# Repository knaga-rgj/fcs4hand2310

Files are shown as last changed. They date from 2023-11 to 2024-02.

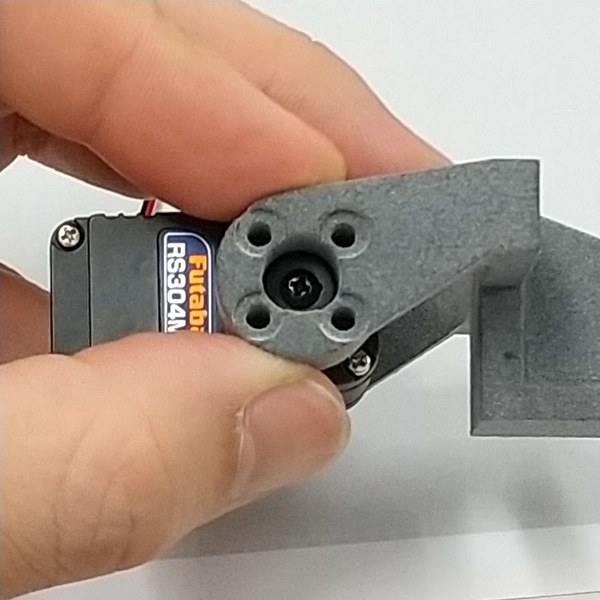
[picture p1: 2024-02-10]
pics/pict11.jpg

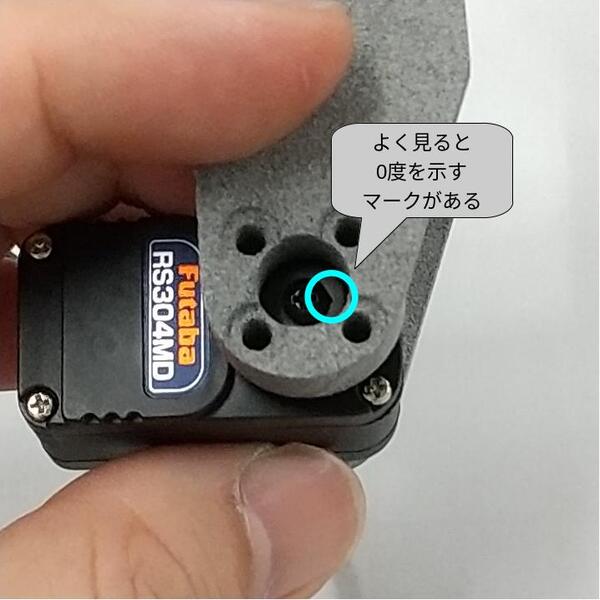
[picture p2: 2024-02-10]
pics/pict08m.jpg

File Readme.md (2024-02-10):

<!-- [GLFM](https://docs.gitlab.com/ee/user/markdown.html)   -->

# fcs4hand2310

## 概要

[双葉電子工業の産業用サーボのコマンド式サーボ](https://www.futaba.co.jp/product/industrial_servo/command_type_servos)を４つ使用するハンドです。

リンク部材は 3D プリンタで作ることを想定しています。（step フォルダ内のデータを活用ください）

ros2_control で制御するために [hardware_fcs](https://github.com/knaga-rgj/hardware_fcs) を使用しています。

各関節角度を joint_trajectory_controller で制御し、joint_state_broadcaster で現在角度を展開するための launch ファイル及び設定ファイル群が用意されています。

humble で動作確認しました。

## 部品一覧

### TTL タイプ

 | 部品名                 | メーカー名   | 型番                                                                                                                                                                                                                                                | 数量   | 備考                                                                                                 |
 |------------------------|--------------|-----------------------------------------------------------------------------------------------------------------------------------------------------------------------------------------------------------------------------------------------------|--------|------------------------------------------------------------------------------------------------------|
 | サーボモジュール       | 双葉電子工業 | [00400021-3 ROBOT SERVO RS304MDFF FUTABA](https://www.futaba.co.jp/product/industrial_servo/command_type_servos/rs304md) もしくは [00400020-3 ROBOT SERVO RS303MRFF](https://www.futaba.co.jp/product/industrial_servo/command_type_servos/rs303mr) | 4      |                                                                                                      |
 | ハブ                   | 双葉電子工業 | [BA2082 TB-RV71EH-7.4V/3W](https://www.futaba.co.jp/product/industrial_servo/command_type_servos/option_parts/relaybox_hub)                                                                                                                         | 1      | 類似型番に注意。末尾「3W」を使用。                                                                   |
 | USB アダプタ           | 双葉電子工業 | [00400070-1 CONVERTER RSC-U485 JPN](https://www.futaba.co.jp/product/industrial_servo/command_type_servos/rsc)                                                                                                                                      | 1      | TB-RV71EH-7.4V/3W とセットで使用（代用不可）                                                         |
 | 電源ケーブル(ハブ側)   | 双葉電子工業 | [BC0079 TB-RV71EH POWER CABLE](https://www.futaba.co.jp/product/industrial_servo/command_type_servos/option_parts/relaybox_hub)                                                                                                                     | 1      | つながれば代用可                                                                                     |
 | EH ４ピンコネクタ      | JST          | [EHR-4](https://www.jst-mfg.com/product/pdf/jpn/EH.pdf)                                                                                                                                                                                             | 4      | ターミネート抵抗を刺すなら１つ追加。                                                                 |
 | EH用コンタクト         | JST          | [(適宜)](https://www.jst-mfg.com/product/pdf/jpn/EH.pdf)                                                                                                                                                                                            | 12     | サーボモジュールは一般的な３ピンで、ハブの４ピンに交換するため。ターミネート抵抗を挿すなら２個追加。 |
 | モータ電源             | (適宜)       | (適宜)                                                                                                                                                                                                                                              | 1      | サーボモジュールは 4.8〜7.2[V] が定格、電流容量は不明                                                |
 | 電源ケーブル（電源側） | (自作)       | (自作)                                                                                                                                                                                                                                              | 1      |                                                                                                      |
 | タッピングネジ         | (適宜)       | (M2 タッピング 10 mm)                                                                                                                                                                                                                               | 34     |                                                                                                      |
 | 両面テープ             | (適宜)       | (薄手のもの)                                                                                                                                                                                                                                        | (適宜) | サーボモジュールとリンク部材との固定は両面テープ                                                     |
 | リンク部材             | (適宜)       | (step ディレクトリ内のを 3D プリント)                                                                                                                                                                                                               | 各1    |                                                                                                      |

工作概略
 - 各サーボモジュールのコネクタを EHR-4 に付け替え
 - リンク部材をサーボホーンにネジ止め
 - リンク部材にサーボモジュールを両面テープで貼り付け
 - 基部のサーボモジュール押さえをネジ止め
 - 電源ケーブル作成（ハブ側、電源側）
 - 配線結線、ID 焼き込み、動作確認
 
注意事項
 - USB アダプタからハブまでは RS-485 なので、ターミネート抵抗を両端に入れると安心できるかもしれません。

### RS-485 タイプ

TTL タイプと比べて RS-485 通信の安心感が増す一方で作業量が増えます。特に DF11 4ピンの配線を間違えると悲惨で危険なことになるかもしれません。

 - サーボモジュールを[外形形状が同じで RS-485 タイプのもの (RS302CD や RS305CR)](https://www.futaba.co.jp/product/industrial_servo/command_type_servos) に変更
 - 軸付きボトムケース [BS3397 RS30x BOTTOM CASE-SHAFT](https://www.futaba.co.jp/product/industrial_servo/command_type_servos/option_parts/servo_caseset) を４つ追加調達
 - フリーホーン（５個セット）[BS0168 RS2xx/RS3xx FREE HORN SET](https://www.futaba.co.jp/product/industrial_servo/command_type_servos/option_parts/servo_horn)を１セット追加調達
 - ハブを[「BA2083 TB-EH31DF-100 もしくは BA2084 TB-EH31DF-200」と「BA2085 TB DF31DF-100」](https://www.futaba.co.jp/product/industrial_servo/command_type_servos/option_parts/relaybox_hub) の２個セットに変更
 - 電源ケーブル（ハブ側）は削除
 - 電源ケーブルを自作（２芯、電源供給側から DF11-4 へ、VCC, GND）
 - 通信用変換ケーブルを自作（３芯、EHR-4 から DF11-4 への変換、D+, D-, GND）

 | 部品名              | メーカー名   | 型番                                                                                                                                                                                                                                   | 数量   | 備考                                                                                                                                                                            |
 |---------------------|--------------|----------------------------------------------------------------------------------------------------------------------------------------------------------------------------------------------------------------------------------------|--------|---------------------------------------------------------------------------------------------------------------------------------------------------------------------------------|
 | サーボモジュール    | 双葉電子工業 | [00400038-1 ROBOT SERVO RS302CDF3 FUTABA ](https://www.futaba.co.jp/product/industrial_servo/command_type_servos/rs302cd) もしくは [00400065-3 RS305CR](https://www.futaba.co.jp/product/industrial_servo/command_type_servos/rs305cr) | 4      |                                                                                                                                                                                 |
 | 軸付きボトムケース  | 双葉電子工業 | [BS3397 RS30x BOTTOM CASE-SHAFT](https://www.futaba.co.jp/product/industrial_servo/command_type_servos/option_parts/servo_caseset)                                                                                                     | 4      |                                                                                                                                                                                 |
 | フリーホーン        | 双葉電子工業 | [BS0168 RS2xx/RS3xx FREE HORN SET](https://www.futaba.co.jp/product/industrial_servo/command_type_servos/option_parts/servo_horn)                                                                                                      | 1      | ５個１セット                                                                                                                                                                    |
 | ハブ（根元側）      | 双葉電子工業 | [BA2083 TB-EH31DF-100 もしくは BA2084 TB-EH31DF-200](https://www.futaba.co.jp/product/industrial_servo/command_type_servos/option_parts/relaybox_hub)                                                                                  | 1      | コネクタを自分で帳尻合わせするなら、創設側と同じ [BA2085 TB DF31DF-100](https://www.futaba.co.jp/product/industrial_servo/command_type_servos/option_parts/relaybox_hub) でも可 |
 | ハブ（増設側）      | 双葉電子工業 | [BA2085 TB DF31DF-100](https://www.futaba.co.jp/product/industrial_servo/command_type_servos/option_parts/relaybox_hub)                                                                                                                | 1      |                                                                                                                                                                                 |
 | USB アダプタ        | 双葉電子工業 | [00400070-1 CONVERTER RSC-U485 JPN](https://www.futaba.co.jp/product/industrial_servo/command_type_servos/rsc)                                                                                                                         | 1      | TB-RV71EH-7.4V/3W とセットで使用します（代用不可）                                                                                                                              |
 | DF11 ４ピンコネクタ | ヒロセ電機   | [DF11-4DS-2C](https://www.hirose.com/ja/product/document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)                                                                                         | 1      | 電源供給ケーブル用。ターミネート抵抗を挿すなら１個追加。                                                                                                                        |
 | DF11用コンタク      | ヒロセ電機   | [(適宜)](https://www.hirose.com/ja/product/document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)                                                                                              | 2      | 同上（ターミネート抵抗を挿すなら２個追加）                                                                                                                                      |
 | モータ電源          | (適宜)       | (適宜)                                                                                                                                                                                                                                 | 1      | サーボモジュールは 4.8〜7.2[V] が定格、電流容量は不明                                                                                                                           |
 | 電源ケーブル        | 自作         | (適宜)                                                                                                                                                                                                                                 |        |                                                                                                                                                                                 |
 | タッピングネジ      | (適宜)       | (M2 タッピング 10mm)                                                                                                                                                                                                                   | 34     |                                                                                                                                                                                 |
 | 両面テープ          | (適宜)       | (薄手のもの)                                                                                                                                                                                                                           | (適宜) | サーボモジュールとリンク部材との固定は両面テープ                                                                                                                                |
 | リンク部材          | (適宜)       | (step ディレクトリ内のを 3D プリント)                                                                                                                                                                                                  | 各1    |                                                                                                                                                                                 |

工作概略
 - 各サーボモジュールのボトムケースを軸付きに交換
   - 配線に目印をつける
   - DF11 ４ピンのハウジングを外す
   - サーボモジュールのボトムケースを交換する
   - DF11 ４ピンのハウジングをとりつける（信号線を挿す場所を間違えないように）
 - リンク部材をサーボホーンにネジ止め
 - リンク部材にサーボモジュールを両面テープで貼り付け
 - 基部のサーボモジュール押さえをネジ止め
 - 電源ケーブル、通信用変換ケーブル作成
 - 配線結線、ID 焼き込み、動作確認

注意事項
 - ターミネート抵抗を RS-485 配線の両端に入れると安心できるかもしれません。
 - ボトムケースを交換する際、DF11 ４ピンコネクタを一旦バラす必要があります。配線の色も同色なため混同しないように細心の注意が必要です。

## 組み立て手順

[写真](./pics/)を参考にしてください。

## 単体動作確認ツール python3 + dicot

[dicot](https://pypi.org/project/dicot/) が便利です。`pip3 install dicot` でインストールできます。
 
[dicot の README.md](https://github.com/lanius/dicot/blob/master/README.md) に目を通した後は、[ソース](https://github.com/lanius/dicot/blob/master/dicot/motors.py) を読むとアクセスしたいプロパティの名称がわかると思います。

シリアルデバイスは dialout group での読み書きが可能なので、Ubuntu の自分自身のユーザアカウントを dialaout グループに追加しておいてください。例えば alice というユーザ名であれば、`sudo adduser alice dialout` を実行し、再起動してください。

### linux で動かす

RSC-U485 は FTDI のドライバ (ftdi_sio) で動きますが、標準の FTDI のドライバには RSC-U485 が登録されていません。手動でその場で動くようにするには以下のコマンドを実行してください。
 
```
$ sudo su
# modrobe ftdi_sio
# echo 1115 0008 > /sys/bus/usb-serial/drivers/ftdi_sio/new_id
```

次回以降の起動時に自動で認識するようにするには、/etc/udev/rules.d 以下に適当な名前のファイルを作成して、以下の記述を書いておいてください。

```
ATTR{idVendor}=="1115", ATTR{idProduct}=="0008", GROUP="dialout", MODE="0660", RUN+="/bin/sh -c '/sbin/modprobe ftdi_sio; /bin/sh -c \"echo 1115 0008\" > /sys/bus/usb-serial/drivers/ftdi_sio/new_id'"
```

### Windows で動かす

多分、ドライバを[Futaba のサイト](https://www.futaba.co.jp/product/industrial_servo/command_type_servos/robot_download/software) からダウンロードしてインストールして、どの COM ポートに割り当てられたか調べて、dicot でその COM ポートを指定すれば動くのではないか、と思います。

## ros2_control で動かすときのコマンドライン覚書

全軸 torque off (inactive 状態へ遷移)

```
ros2 service call /controller_manager/set_hardware_component_state controller_manager_msgs/srv/SetHardwareComponentState "{name: fcs0, target_state: {id: 0, label: inactive}}"
```

全軸 torque enable (active 状態へ遷移)

```
ros2 service call /controller_manager/set_hardware_component_state controller_manager_msgs/srv/SetHardwareComponentState "{name: fcs0, target_state: {id: 0, label: active}}"
```

目標角度へ動作（ここでは [0, 0, 0, 0], 単位はラジアン）

```
ros2 action send_goal /joint_trajectory_controller_fcs4hand2310/follow_joint_trajectory control_msgs/action/FollowJointTrajectory -f "{ trajectory: { joint_names: [ hndj0, hndj1, hndj2, hndj3 ], points : [ { positions: [0, 0, 0, 0], time_from_start: { sec: 0.5 }} ]}}"
```

## このリポジトリについて

 | ファイル名                                | 概要                                                                                       |
 |-------------------------------------------|--------------------------------------------------------------------------------------------|
 | launch/fcs4hand2310.launch.py             | launch スクリプト。ros2_control の設定もコーディングされています                           |
 | urdf/fcs2310.urdf                         | 軸配置と外形を記述。プレビューで使用。                                                     |
 | urdf/fcs4hand2310ctrl.xacro               | トップレベル URDF。fcs2310.urdf を読み込んで、ros2_control タグ、hardware_fcs タグを追加。 |
 | config/ros2_controllers_fcs4hand2310.yaml | joint_trajectory_controller と joint_state_broadcaster の設定                              |
 | step/*                                    | リンク部材の STEP ファイル (ros2_control で動かすのには不要)                                                                 |
 | pics/*                                    | 組み立て中の写真 (ros2_control で動かすのには不要)                                                                          |

スクリプトファイル群
 | ファイル名       | 概要                                                                                                                                                 |
 |------------------|------------------------------------------------------------------------------------------------------------------------------------------------------|
 | torque_free.sh   | ex_fcs0 (HardwareFCS) を inactive 状態にする。on_deactive() 処理中に全サーボにサーボオフ (Torque Enable = False) が送られる。                        |
 | torque_enable.sh | ex_fcs0 (HardwareFCS) を active 状態にする。on_activate() 処理中に指令値を現在値で上書きし、全サーボにサーボオン (Torque Eanble = True) が送られる。 |
 | set_angles.py    | joint_trajectory_controller_fcs4hand2310 (JointTrajectoryController) に動作指令を送る。python から `ros2 action send_goal ...` を実行している(手抜き) |

```
├── CMakeLists.txt
├── Readme.md
├── config
│   └── ros2_controllers_fcs4hand2310.yaml
├── launch
│   └── fcs4hand2310.launch.py
├── package.xml
├── pics
│   ├── pict00.jpg
│   ├── pict01.jpg
│   ...
├── step
│   ├── FCS4HAND2310_BASE.STEP
│   ├── FCS4HAND2310_BASE_LID.STEP
│   ...
├── scripts
│   ├── set_angles.py
│   ├── torque_enable.sh
│   └── torque_free.sh
└── urdf
    ├── RS30x_BottomShaft.dae
    ├── fcs4hand2310.xacro
    └── fcs2310.urdf
```

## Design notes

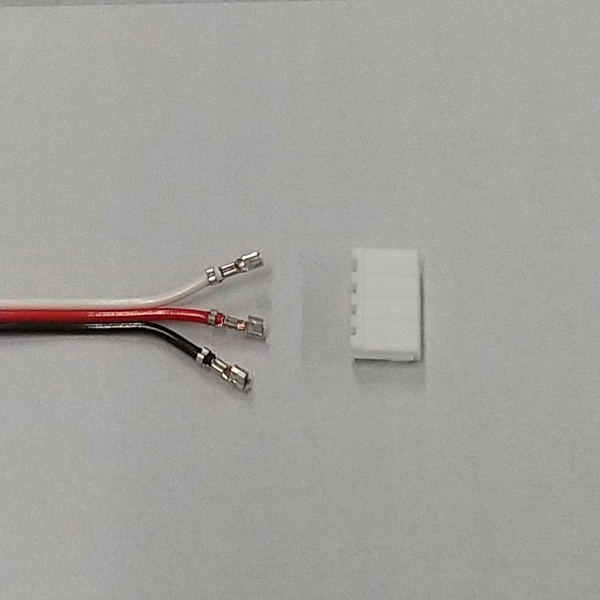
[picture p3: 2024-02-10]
pics/pict02.jpg

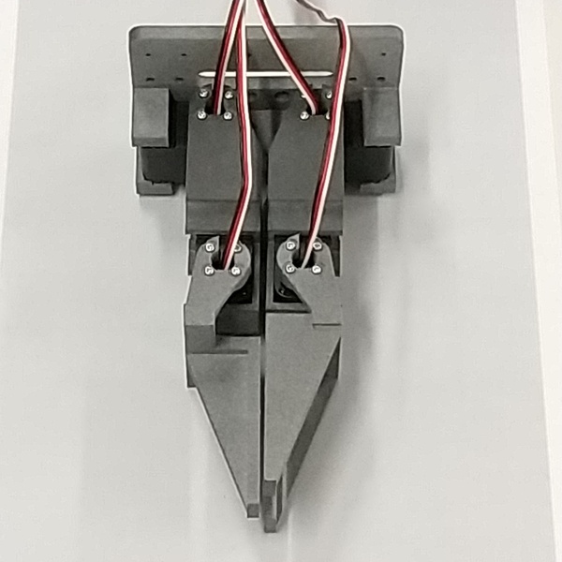
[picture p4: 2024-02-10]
pics/pict15.jpg

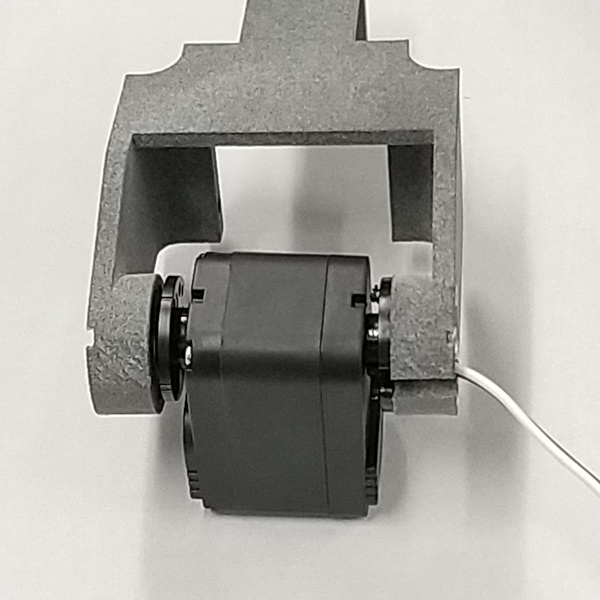
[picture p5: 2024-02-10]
pics/pict07.jpg

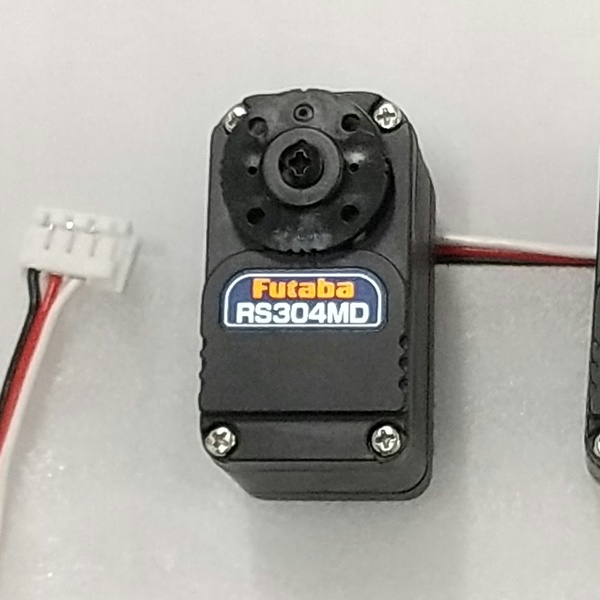
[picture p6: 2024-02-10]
pics/pict04.jpg

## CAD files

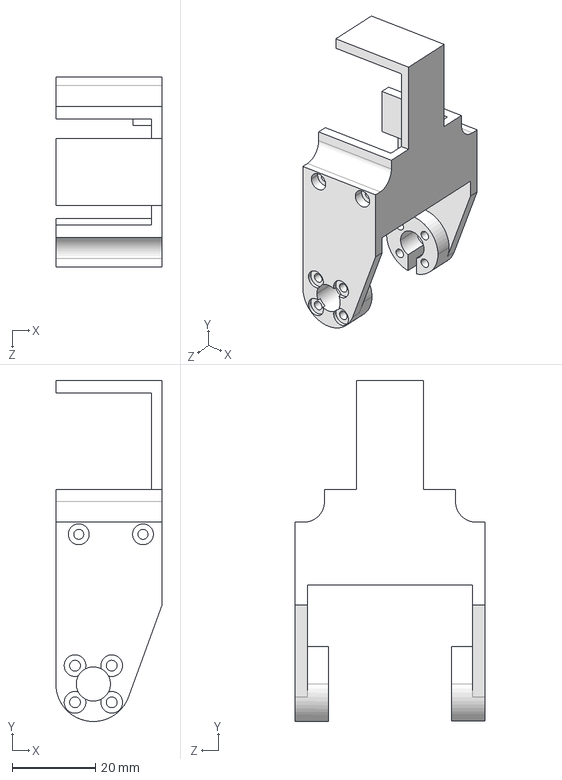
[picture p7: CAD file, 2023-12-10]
step/FCS4HAND2310_FINGER_ROOT_RH.STEP
25.5 x 81.8 x 45.6 mm

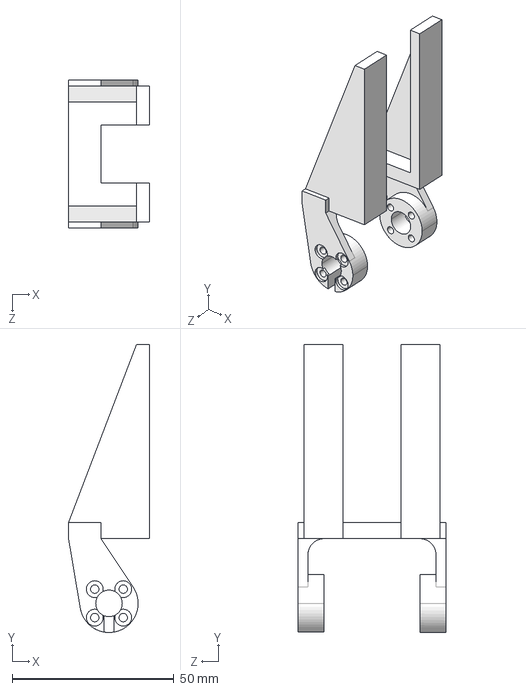
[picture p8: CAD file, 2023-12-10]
step/FCS4HAND2310_FINGER_EDGE_LH.STEP
25.0 x 89.0 x 45.6 mm

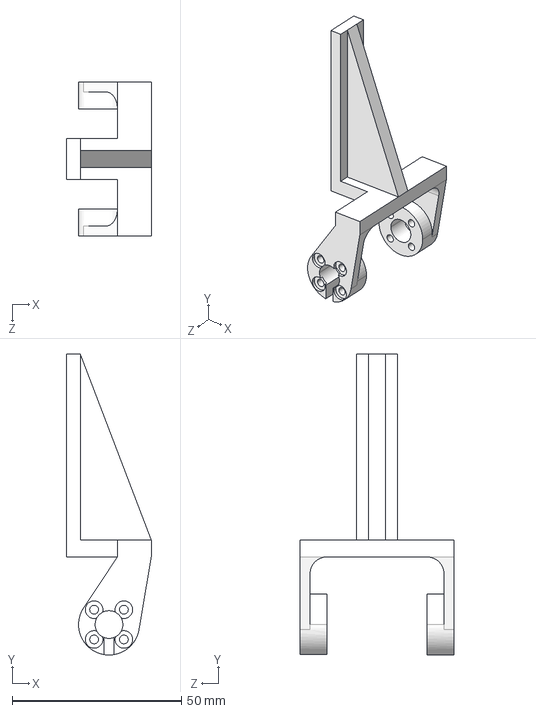
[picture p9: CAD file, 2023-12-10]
step/FCS4HAND2310_FINGER_EDGE_RH.STEP
25.0 x 89.0 x 45.6 mm

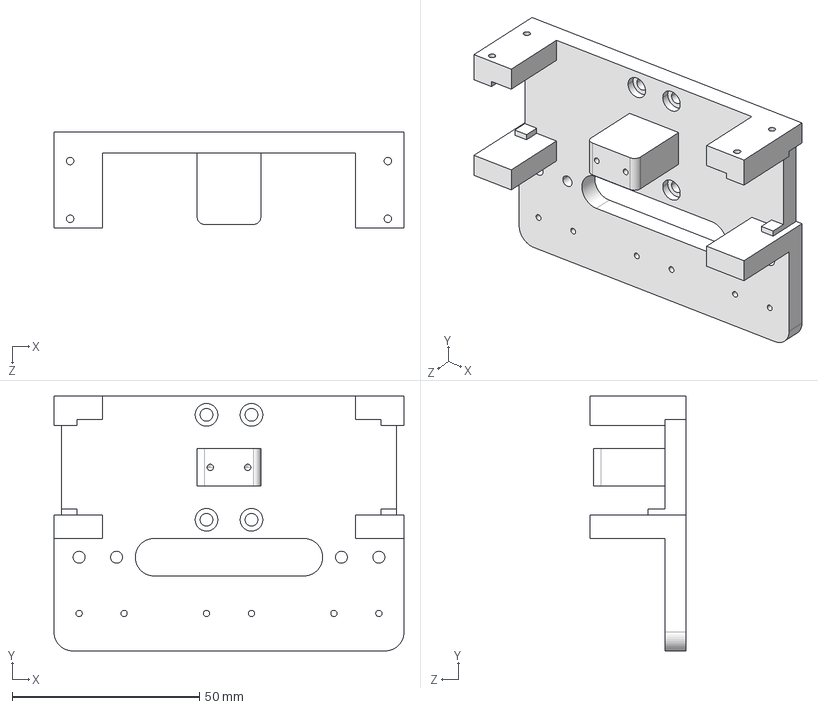
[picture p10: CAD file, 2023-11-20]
step/FCS4HAND2310_BASE.STEP
93.4 x 68.0 x 25.7 mm

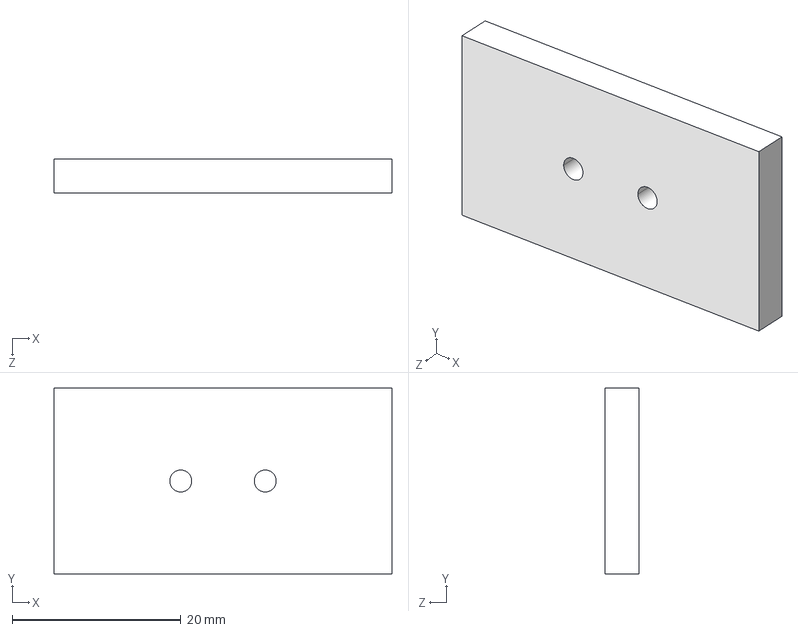
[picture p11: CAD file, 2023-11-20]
step/FCS4HAND2310_BASE_LID.STEP
40.0 x 22.0 x 4.00 mm

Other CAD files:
step/FCS4HAND2310_FINGER_ROOT_LH.STEP

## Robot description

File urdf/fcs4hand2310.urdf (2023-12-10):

<?xml version="1.0"?>
<robot name="fcs2310">
  <link name="base">
    <visual name="base plate">
      <!-- <origin xyz="0.002 0 -0.01" /> -->
      <!-- <geometry> -->
      <!-- 	<box size="0.004 0.1 0.07"/> -->
      <!-- </geometry> -->
      <origin xyz="0 0 0.0022" rpy="-1.57079632675 0 -1.57079632675"/>
      <geometry>
	<mesh filename="package://fcs4hand2310/urdf/FCS4HAND2310_BASE.dae"/>
      </geometry>
      <material name="gray80">
	<color rgba="0.8 0.8 0.8 1.0"/>
      </material>
    </visual>
    <visual name="R30xxx (J00)">
      <origin xyz="0.060 -0.0358 0.035" rpy="0 0 1.57079632675"/>
      <geometry>
	<mesh filename="package://fcs4hand2310/urdf/RS30x_BottomShaft.dae"/>
      </geometry>
      <material name="blue">
	<color rgba="0.0 0.0 1.0 1.0"/>
      </material>
    </visual>
    <visual name="R30xxx (J10)">
      <origin xyz="-0.030 0.0356 0.035" rpy="0 0 -1.57079632675"/>
      <geometry>
	<mesh filename="package://fcs4hand2310/urdf/RS30x_BottomShaft.dae"/>
      </geometry>
      <material name="blue"/>
    </visual>
    <visual name="base LID">
      <origin xyz="0.025 0 0" rpy="1.57079632675 0 1.57079632675"/>
      <geometry>
	<mesh filename="package://fcs4hand2310/urdf/FCS4HAND2310_BASE_LID.dae"/>
      </geometry>
    </visual>
  </link>
  <link name="FG00">
    <visual name="FG00">
      <!-- <origin xyz="0.030 0.015 0.0"/> -->
      <!-- <geometry> -->
      <!-- 	<box size="0.060 0.003 0.040"/> -->
      <!-- </geometry> -->
      <origin xyz="0.0 0.033 0.025" rpy="3.141592653589793 0 1.57079632679489661923"/>
      <geometry>
	<mesh filename="package://fcs4hand2310/urdf/FCS4HAND2310_FINGER_ROOT_RH.dae"/>
      </geometry>
      <material name="gray80">
	<color rgba="0.8 0.8 0.8 1.0"/>
      </material>
    </visual>
    <visual name="RS3xxx (J01)">
      <origin xyz="0.0425 -0.041 0.035" rpy="0 0 0"/>
      <geometry>
	<mesh filename="package://fcs4hand2310/urdf/RS30x_BottomShaft.dae"/>
      </geometry>
      <material name="blue"/>
    </visual>
  </link>
  <link name="FG01">
    <visual name="FG01">
      <!-- <origin xyz="0.05 0.011 0.0"/> -->
      <!-- <geometry> -->
      <!-- 	<box size="0.050 0.003 0.015"/> -->
      <!-- </geometry> -->
      <origin xyz="0.0 0.0 -0.020" rpy="0 0 -1.57079632679489661923"/>
      <geometry>
	<mesh filename="package://fcs4hand2310/urdf/FCS4HAND2310_FINGER_EDGE_RH.dae"/>
      </geometry>
      <material name="gray80"/>
    </visual>
  </link>
  <link name="FG10">
    <visual name="FG10">
      <!-- <origin xyz="0.03 -0.015 0.0"/> -->
      <!-- <geometry> -->
      <!-- 	<box size="0.06 0.003 0.04"/> -->
      <!-- </geometry> -->
      <origin xyz="0.0 0.0 0.025" rpy="3.141592653589793 0 1.57079632679489661923"/>
      <geometry>
	<mesh filename="package://fcs4hand2310/urdf/FCS4HAND2310_FINGER_ROOT_LH.dae"/>
      </geometry>
      <material name="gray80"/>
    </visual>
    <visual name="RS3xxx (J11)">
      <!-- <origin xyz="0.0425 -0.041 0.035" rpy="0 0 0"/> -->
      <origin xyz="0.0425 -0.049 0.035" rpy="0 0 0"/>
      <geometry>
	<mesh filename="package://fcs4hand2310/urdf/RS30x_BottomShaft.dae"/>
      </geometry>
      <material name="blue"/>
    </visual>
  </link>
  <link name="FG11">
    <visual>
      <!-- <origin xyz="0.05 -0.011 0.016"/> -->
      <!-- <geometry> -->
      <!-- 	<box size="0.050 0.003 0.012"/> -->
      <!-- </geometry> -->
      <origin xyz="0.0 0.005 -0.020" rpy="0 0 -1.57079632679489661923"/>
      <geometry>
	<mesh filename="package://fcs4hand2310/urdf/FCS4HAND2310_FINGER_EDGE_LH.dae"/>
      </geometry>
      <material name="gray80"/>
    </visual>
    <visual>
      <origin xyz="0.05 -0.011 -0.016"/>
      <geometry>
	<box size="0.05 0.003 0.012"/>
      </geometry>
      <material name="gray80"/>
    </visual>
  </link>
  <!-- <link name="hub31x2"> -->
  <!--   <visual name="TB-DF31DF (1/2)"> -->
  <!--     <origin xyz="0 -0.023 0" rpy="0 0 0"/> -->
  <!--     <geometry> -->
  <!-- 	<box size="0.012 0.040 0.014"/> -->
  <!--     </geometry> -->
  <!--     <material name="gray40"> -->
  <!-- 	<color rgba="0.4 0.4 0.4 1.0"/> -->
  <!--     </material> -->
  <!--   </visual> -->
  <!--   <visual name="TB-DF31DF (2/2)"> -->
  <!--     <origin xyz="0 0.023 0" rpy="0 0 0"/> -->
  <!--     <geometry> -->
  <!-- 	<box size="0.012 0.040 0.014"/> -->
  <!--     </geometry> -->
  <!--   </visual> -->
  <!-- </link> -->
  <link name="hub71">
    <visual name="TB-RV71EH (body)">
      <!-- <origin xyz="0.009 -0.010 -0.030" rpy="0 0 0"/> -->
      <origin xyz="0 0 0" rpy="0 0 0"/>
      <geometry>
	<box size="0.020 0.062 0.014"/>
      </geometry>
      <material name="gray40">
	<color rgba="0.4 0.4 0.4 1.0"/>
      </material>
    </visual>
    <visual name="TB-RV71EH (switch)">
      <!-- <origin xyz="0.012 -0.024 -0.024" rpy="0 0 0"/> -->
      <origin xyz="0.003 0.014 0.006" rpy="0 0 0"/>
      <geometry>
	<box size="0.006 0.014 0.020"/>
      </geometry>
      <material name="gray40"/>
    </visual>
  </link>
  <!-- <link name="PET bottle"> -->
  <!--   <visual> -->
  <!--     <geometry> -->
  <!-- 	<cylinder length="0.230" radius="0.035"/> -->
  <!--     </geometry> -->
  <!--     <material name="orange"> -->
  <!-- 	<color rgba="1.0 0.647 0.0 1.0"/> -->
  <!--     </material> -->
  <!--   </visual> -->
  <!-- </link> -->
  <joint name="hndj00" type="revolute">
    <origin xyz="0.0155 -0.0175 0.0"/>
    <axis xyz="0 0 1"/>
    <parent link="base"/>
    <child link="FG00"/>
    <limit effort="30" velocity="1.0" lower="-1.57079632679489661923" upper="0"/>
  </joint>
  <joint name="hndj01" type="revolute">
    <origin xyz="0.061 0.004 0.0"/>
    <axis xyz="0 0 1"/>
    <parent link="FG00"/>
    <child link="FG01"/>
    <limit effort="30" velocity="1.0" lower="-2.61799387799149436538" upper="2.61799387799149436538"/>
  </joint>
  <joint name="hndj10" type="revolute">
    <origin xyz="0.0155 0.0175 0.0"/>
    <axis xyz="0 0 1"/>
    <parent link="base"/>
    <child link="FG10"/>
    <limit effort="30" velocity="1.0" lower="0" upper="1.57079632679489661923"/>
  </joint>
  <joint name="hndj11" type="revolute">
    <origin xyz="0.061 -0.004 0.0"/>
    <axis xyz="0 0 1"/>
    <parent link="FG10"/>
    <child link="FG11"/>
    <limit effort="30" velocity="1.0" lower="-2.61799387799149436538" upper="2.61799387799149436538"/>
  </joint>
  <!-- <joint name="hub" type="fixed"> -->
  <!--   <origin xyz="0.013 0 0.040" rpy="0 1.57079632679489661923 0"/>  -->
  <!--   <parent link="base"/> -->
  <!--   <child link="hub31x2"/> -->
  <!-- </joint> -->
  <joint name="hub" type="fixed">
    <origin xyz="0.013 0 0.041" rpy="0 1.57079632679489661923 0"/>
    <parent link="base"/>
    <child link="hub71"/>
  </joint>
  <!-- <joint name="PET bottle" type="fixed"> -->
  <!--   <origin xyz="0.068 0 0"/> -->
  <!--   <parent link="base"/> -->
  <!--   <child link="PET bottle"/> -->
  <!-- </joint> -->
  
</robot>

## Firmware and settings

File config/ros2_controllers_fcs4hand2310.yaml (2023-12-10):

joint_state_broadcaster_fcs4hand2310:
  ros__parameters:
    joints: [ hndj00, hndj01, hndj10, hndj11 ]
    interfaces: [ position ]

joint_trajectory_controller_fcs4hand2310:
  ros__parameters:
    joints: [ hndj00, hndj01, hndj10, hndj11 ]
    command_interfaces: [ position ]
    state_interfaces:   [ position ]
    state_publish_rate:   2.0 # Defaults to 50
    action_monitor_rate:  2.0 # Defaults to 20
    allow_partial_joints_goal: false # Defaults to false
    open_loop_control: true
    allow_integration_in_goal_trajectories: true
    allow_nonzero_velocity_at_trajectory_end: false
    constraints:
      stopped_velocity_tolerance: 0.01 # Defaults to 0.01
      goal_time: 0.0 # Defaults to 0.0 (start immediately)
